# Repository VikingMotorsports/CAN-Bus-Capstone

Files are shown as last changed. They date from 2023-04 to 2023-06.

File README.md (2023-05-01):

<p align="center">

</p>

# VMS Can Bus Sensor Array

## Proposal Outline and Discussion

### 1. Executive Summary
Viking Motorsports is an EV racing team at PSU. They are a student organization and compete in
the Formula SAE competition against other schools nationally. Their overall goal is to design,
build and race a car every year. The electrical systems are complex, there are many systems that
must work in harmony with each other. There are also many possible single point failures that
can occur that will end our race.
Understanding this complex system is difficult, all of the information is locked away behind
body panels and wire insulation. The motivation of this project is to tap into that data to make it
easily accessible, this will enable rapid diagnostics and debugging. Additionally valuable data is
encoded in CAN by various off the shelf systems within the car. Accessing this data will also be
beneficial.
We want to deliver a network system that uses CAN to communicate system analytics from the
car's batteries and several other measured components and relay that information to the driver’s
display screen. The analytics will help troubleshoot any faults and errors in the operation of the
vehicle and allow for faster fixes on the race track. The system overall will consist of multiple
PCBs mounted in various locations on the vehicle to allow for sensor wires to relay the data to be
sent from each component to a data analyzer then get displayed on the screen.

<p align="center">

</p>

### 2. Background
The Viking Motorsports Team at PSU has been working on creating a fast, efficient, and
innovative EV to participate in the FSAE competition. Our project involves monitoring several
aspects of the EV via CAN and displaying the sensor outputs to the screen in the vehicle.
Monitoring these aspects via CAN will allow for efficient diagnostics of the EV systems and
make way for troubleshooting in the event of any failures.
The current electrical system is represented in the following diagram.

<p align="center">

</p>

For simplicity, all low voltage connections have been omitted, as well as some minor systems.
Currently, the only monitoring that is being done is battery temperature, and all monitoring done
by off the shelf systems within their own system. None of this information is accessible without
connecting a laptop to the various systems directly.
There are several different systems that need monitoring inside the EV. Primarily the HV (High
Voltage) system requires monitoring of the temperature sensors for the compartments that hold
the batteries. The temperature of the batteries affects the power output as well as the overall
performance of the car. Other components include the accumulator isolation relays, fuse, current
sensors, precharge and discharge system. The EV also requires monitoring of the LV (Low
Voltage) systems as well as the status of the pedal control system.
The industry standards have several requirements for CAN protocols being utilized in road
vehicles. Some of them include the following form ISO 11898:

* CAN specifies the high-speed physical media attachment (HS-PMA), including
HS-PMAs without and with low-power mode capability and those with selective wake-up
functionality.
* CAN specifies characteristics of setting up an interchange of digital information between
electronic control units of road vehicles equipped with CAN.

* CAN specifies the characteristics of setting up an interchange of digital information
between modules implementing the protocol’s data link layer.
Being able to monitor, process, and display these systems statuses will be extremely beneficial
for troubleshooting and overlay monitoring of the EV. The Formula SAE competition has very
specific requirements regarding galvanic isolation of the HV and LV systems in the EV. These
requirements need to be followed when developing our CAN system.

Data Flow Diagram
<p align="center">

</p>

It is important to note that the VMS team has not utilized the CAN bus system for monitoring
any sensor outputs in the past. However, even though the team has not implemented this system
yet, there are several other off the shelf devices that utilize CAN to help monitor and also
provide ability to alter the sensors and their calibration in order to get the best outcome from the
overall system. Haltech offers a wide range of CAN Bus devices along with the sensors that are
heavily used in the automotive industry, especially in DIY projects where factory engine
management systems fail to deliver proper results. Research in companies like Haltech as well as
other products like Vector used by Daimler can be beneficial for our project as well.

### 3. Project Overview
Our project starts with getting the STM32s to communicate with each other in order to relay information 
from one device to another. Each STM32 in our network will act as a CAN hub
utilized to relay information from a specific component cluster on the vehicle. We then want to
determine the protocols that allow data from the sensors to be received through the CAN
transceivers.

We then have to design individual PCBs for each of the CAN hubs that hold the STM32s, the
CAN transceivers and other peripheral components for the sensors to operate on the vehicle as
well.

Using the STM32CubeIDE and C programming, we have to code each of the microcontrollers to
log the data received from the CAN transceivers and relay them to the main Data Translator hub.
The Data Translator further encodes the data to be read by a RaspberryPi via I2
C which is used to display the data on the screen. We want the CAN system to be able to 
collect sensor outputs from different components of the
EV, send them to a central control hub, which processes the sensor readouts to legible
information for the user and outputs to a screen via the CAN adapter.

### 4. Product Design Specification

#### 4.1 Concept of Operation / User stories
Our goal for this project is to provide several different CAN modules that can be connected to
different sensors on the EV components and the placement of these modules provides flexibility
and easy integration along with the rest of the parts on the EV. Since the EV has restraints for
weight, countless other things, the placement of our modules is very important. These modules
are connected to the sensors on the vehicle and thus take the sensor readouts when the EV is
operated. The CAN module thus sends the readouts to the central control hub which is another
module that we create. This central hub encodes the sensor outputs and then sends them to the
LCD display on the car via a CAN Adapter.

As mentioned earlier, these modules are constructed specifically for the VMS EV and would for
the most part only work for our specific application since the placement on the devices, types of
sensor, variation in sensor outputs and the process to encode them would vary from one vehicle
to another. Thus the VMS team and their intermediate sponsors would be our main users and
stakeholders in this project.

It is important to note that the vehicles built by the VMS team in the past have not had any CAN
bus system utilized for monitoring and diagnostics. All previous troubleshooting was done in the
event of a system failure and the panels had to be taken apart to look at the individual
components and sensors to determine the source of error. The CAN bus allows the electricians on
the VMS team to simply use the LCD display and examine the readouts from the sensor in the
event of the failure. This speeds the time it takes them to fix the car and get it back in the race at
the FSAE competition. At the time the scope of our design concludes with relaying the data on
the display screen. However, the project can be continued in the future to use the CAN Adapter
to output the data logs to a laptop. There is also room in the future to be able to act upon the
information received via CAN. For example, the ability to do system shutdown in the event of a
component failure or out of range sensor reading can be a very effective addition to the overall
safety of the vehicle.

In our case, since the sponsor is the primary user for our project, we want to follow the timeline
of the rest of the EV build. Although we are not able to act upon the readouts we get from the
sensor, we are merely monitoring them. However, there are products available in the market that
allow for calibration and adjustment via USB connection to the CAN and sensors. This can be
looked into upon future development of our project. Each of the CAN hubs will also act as data
loggers as the microcontrollers will pull the data from the CAN bus, hold and store it.

As the rest of the members on the VMS team work on the other components that make the EV
work, we want to work alongside their progress so as to make the integration of the CAN Bus
more efficient and avoid any delays. We want the individual modules of the CAN Bus to be a
plug and play system which can be routed along with the rest of the wiring on the EV. Although
the design of the CAN Bus will be new for this year's EV, considering the fact that the VMS
team has to build a new vehicle from scratch every year, they might be able to utilize some of the
code and hardware and expand on the design of the CAN Bus for any future builds. Our goal is
to create a smoothly integrated monitoring system system that is seamless with the rest of the EV
build.

#### 4.2 Stakeholders
Our project was proposed by Braeden Hamson, lead electrician on the VMS team. Him, along
with several other key members on the team have been putting in countless hours in researching,
developing, constructing, testing, and then improving the iterations of the EV. We are designing
and constructing the CAN bus based on their requirements and working with them to create
smooth integration of the CAN Bus into the EV. However we feel that there can be several other
stakeholders in our project. The project team including Alice Ma, Braeden Hamson,
Jade Nguyen, and Pushpesh Sharma, want to create something that leaves room for future
growth and improvement. The EV inspectors that are part of the FSAE competition should also
be considered solid stakeholders in this project as their judgment and criticism can be beneficial
to the development of our project. But for the most part, the EV team at PSU will help integrate
its system, utilize it during the testing phase of the vehicle as well as on the track during the
competition. Upon the success of this project, we hope that the VMS team is able to use the
system for future use and add more features that helps the EV perform better in the upcoming
competitions.

#### 4.3 Requirements and Specifications
As mentioned earlier, we want to adhere to the requirements of the EV overall when designing
and constructing our CAN Bus systems. We want to follow any necessary restraints set by the
FSAE competition guidelines so as to avoid any delays and provide smooth integration of our
systems with the rest of the vehicle. Thus most of our requirements for this project are based on
the number of sensors and components that we want to read and monitor for the management of
the EV. Other requirements are based on what components we utilize in our project in order to
stay on budget and provide smooth integration when the time comes.

* Must be powered from 12V and/or 5V and tolerate a +/- 2V fluctuation
* When a board interacts with HV (350VDC) all HV components must be galvanically isolated from LV systems
* Must send data to a central data logging device connected to the CAN Bus
* Must use appropriate CAN Bus arbitration
* The team must cooperate with other members of the VMS team to ensure system compatibility
* Should follow accepted methods to protect devices on a CAN Bus
* Should use STM32 microcontrollers
* May monitor status of shutdown switches
* Should transmit data at a rate appropriate for the specific measurement
* Should monitor the following systems, in order of priority:
  * AIR+, AIR-, and precharge signals
  * APPS, BSPD, IMD, BMS OK, SDC status
  * Tractive system voltage, tractive system current
  * LV system voltages
  * Orion BMS 2 data
    * Battery state of charge
    * Tractive system power output
    * Battery voltage
    * Battery current
  * Cascadia Motion PM100DX data
    * Individual motor power
    * Inverter mode (running, fault, precharging etc.)
    * Relay outputs (used to detect wiring faults)

#### 4.4 Deliverables
This critical section specs out what you're going to deliver to the industry sponsor by the end of
your capstone. This must include:

* Project proposal
* Weekly Progress Reports
* Final Report
* ECE Capstone Poster Session poster
* Travel with the VMS team to Michigan to attend the FSAE competition. It is held on June 14-17 (travel and other expenses are covered)
* Detailed design documentation, explaining how your what your design does, how your design works, and why you made the decisions you did
* Simulations, including both the simulation inputs and outputs
* Electrical CAD: Schematics and board layouts, including output files (Gerbers, PDFs, etc)
* Bill of materials and pricing
* Version control, including checked in previous revisions of your design (e.g., a Git repo).
* Individual PCBs with 3D printed housings for each of the boards.
* Functional code for STM32CubeIDE for the individual CAN hubs.

#### 4.5 Initial product design
Our current progress on this project consists of setting up software for the microcontroller
that we will be using. We have decided to use STM32 along with the STM IDE to be able
to take the sensor outputs from each component and then convert the values to send to the
CAN Adapter which in the end gets displayed on the screen. We have also started
working on the schematics for the PCBs that contain the STM32 microcontroller. These
schematics contain the microcontroller itself along with the peripheral components that
are necessary. We are also working on getting multiple STM32s to communicate with
each other as the end goal would be to have several different boards placed in close
proximity to the location of the sensor and have them send the sensor output to one main
microcontroller board via CAN that processes the input and sends it to the CAN adapter.

* Hardware architecture
<p align="center">

</p>

* Software architecture
  * C, STM32CubeIDE

* User interface / experience

User Story: In the lab, the user is assembling the car, they test a certain feature
and see that it does not function as intended. They can then go to the driver’s
steering wheel, use the on wheel controls to enter a maintenance menu that will
display all measured parameters by the CAN system. They can then use this
information to find the problem. For instance, the car is powered on, but HV will
not engage. The user looks at the data from the wheel and sees that the pedal
control board is indicating a signal out of range of the pedal controller.
Investigating the sensor connections they find the sensor unplugged. They plug
the sensor in and the system indicates the sensor is in range. The car then turns on.

* Other considerations

Electric vehicles are electrically noisy. Shielded wire will be used for long wire
runs around the vehicle.
The battery pack contains up to 350V, galvanic isolation will separate the boards
that are close to HV systems from the rest of the systems.

* Back up plans

The overall goal of this project is to create an easily debugged vehicle. If our
plans totally crash and burn there’s nothing wrong with creating a 1960’s aesthetic
by throwing a ton of blinking indicators around the car for debugging.
A step up from that is to use Arduinos and create a similar but less complex
system for debugging.
The only aspect of this project that must be completed are the battery temperature
monitors. Without this system the vehicle will not be allowed to race.

#### 4.7 Verification plans
One of the biggest concerns with this project is the final integration of the CAN Bus with the rest
of the components on the EV. We want to make sure that the system is able to successfully take
the readouts from the sensors on the EV and encode them to be displayed on the screen. A lot of
testing would be required to determine that the system is operating correctly.

The system will meet requirements if it can successfully read the temperature sensors in the
battery modules and display them on the LCD. We may program the STM32s to encode the
readout from the temperature sensors and determine whether it falls within the specific range for
the battery to have optimal performance based on the requirements of the VMS team. Test: Does
the LCD display the temperature of the specific battery module? Does it indicate when the
temperature gets above a threshold range?

We are also going to test multiple STM32s to see if they can communicate with each other
through the CAN network by sending messages from component A to component B, then from
component B to component C, or until one goes to bus-off condition. we will determine if the
system can analyze the error registers of the node as a means of measuring bus performance of a
transceiver.

### 5. Project Management Plan

#### 5.1 Timeline, with milestones
The timeline for our project needs to be aligned with that of the VMS team in order to finish the
EV in time for the FSAE competition. Our sponsor wants to have a working CAN Bus system by
the end of the ECE 412 course in order to leave ample time for system integration with the rest
of the EV as well as the testing, and troubleshooting phases.
See Google Sheets below for a tentative timeline

Click [here](https://docs.google.com/spreadsheets/d/1ESAUExDIhOSoRCvXFfbeXnNjUjRd7T-Y1ovpI8qUFuQ/edit#gid=0) to view tentative project timeline

#### 5.2 Budget and Resources

The budget for our project is combined with that of the overall VMS budget for the EV. Our
main costs are going to dependent on the following:

● Number of STM32s used and their cost
● Cost of peripheral components for the microcontrollers
● Manufacturing costs of the PCBs for the STM32s and the peripheral components
● Wiring for the integrated boards via CAN.

The VMS team has kindly Altium to design the PCBS for the CAN modules. Most other
components would be ordered from DigiKey or may already be available in the VMS inventories
as they have been working on multiple vehicles in the past. The VMS team has also provided a
work area along with the rest of the team members as resources for our project.

#### 5.3 Intellectual Property Discussion
A goal of this capstone is to provide a framework to future teams to build more advanced CAN
systems. Therefore all IP generated here will be completely open source, and will be readily
available to future teams. The license used for the repository and the project overall is the MIT License
<p>

</p>

#### Faculty Advisor Approval
Advisor Name: Roy Kravitz |
Signature: e-approved by Roy Kravitz (rkravitz@pdx.edu) |
Date: 27-Feb-2023

#### 5.4 Team and Development process

* Alice Ma: Project manager and Programming lead. Working on programming STM32 for
sending and receiving CAN messages.
* Braeden Hamson: VMS electrical lead. CAN capstone technical lead. Understands the
vehicle systems and the interface between the CAN system and the rest of the systems of
the car.
* Jade Nguyen: Working with Alice on setting up a CAN bus using the STM32
microcontroller, providing simple C code to read and write to the CAN bus and send it to
the transceiver.
* Pushpesh Sharma: Working on PCB schematics and using Altium to set up schematics,
footprints, PCB files and manufacturing files for several boards for CAN Bus.

* Collaboration tools: Notion for team tasking and note taking, Discord for every comms
and virtual meetings, Github for code and boards, Google Suite for deliverables.

### Project Sponsor 

<p align="center">

</p>

Viking Motorsports (VMS) is a student group focused on designing and building formula race
cars from the ground up. Every year, VMS competes in Formula SAE, which is a worldwide
collegiate competition created by SAE International.

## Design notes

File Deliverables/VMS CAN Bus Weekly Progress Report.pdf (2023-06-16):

### VMS CAN Bus Capstone Weekly Progress Report

Report date: Jan 20, 2023

- Last Week (times in hours)
- Team Review
■ We planned for a short check-in meeting on Mondays and a working meeting on Thursday.
■ Had a meeting with the faculty advisor.
■ Gave everyone a role for the project.
■ Got into the VMS lab to look at the physical car and get supplies (STM32) needed to start coding.
- Braeden Hamson
■ Contacted, via email, the faculty advisor, Roy, to introduce us as a team (0.5)
■ Gathered a list of sensors we need to get signals from (2)
■ Researched about the STM32 (2)
- Pushpesh Sharma
■ Researched about CAN (3)
- Alice Ma
■ Planned our meetings with Roy via email (.5) ■ Researched about CAN (3)
- Jade Nguyen
■ Researched about CAN (3)
- Next week
- Team Plan
■ Meeting with sponsors (other VMS team members) in person to get their opinion and requirements on the project.
- Braeden Hamson
■ Order STM32 enough for the project (1)
■ Gathered a list of sensors we need to get signals from (2)
■ Start testing the CAN transceivers and STM32 for sending CAN messages.
- Pushpesh Sharma
■ Set up our collaboration site on Github and added structure (3)
■ Learn about Altium (3)
- Alice Ma
■ Start programming the STM32 and get familiar with the IDE (3)
■ Planned meeting with faculty advisor for bi-weekly Friday meetings (.25) ■ Start the template for the weekly progress reports. (1)
- Jade Nguyen
■ Learn about CAN protocol (3)
■ Start programming the STM32 and get familiar with the IDE (3)
- Blocked
- Braeden Hamson
■ Need to wait until more STM32 to get here so we can all start programming.
- Pushpesh Sharma
■ Haven’t gotten access code for the Altium program
- Alice Ma
■ No blocks
- Jade Nguyen
■ No blocks

Report date: Jan 27, 2023

- Last Week (times in hours)
- Team Review
■ Originally planned to have a central STM32 that collected a lot of the data, but now we will use Raspberry pi.
■ Everyone has done good basic research of the topic
- Braeden Hamson
■ Tested the STM32 boards and CAN transceivers (3) ■
- Pushpesh Sharma
■ Finished with Altium tutorials (3)
■ Started Altium files for Accumulator Schematic.
- Alice Ma
■ Was able to write code to the STM32 board (3)
- Jade Nguyen
■ Researched about CAN (3)
- Next week
- Team Plan
■ We should divide our time as the programming team and the circuit design team.
- Braeden Hamson
■
- Pushpesh Sharma
■ Design schematics, collect part specs for connectors and mates, work on symbol and footprint of STM32. Find the thermistor part. Design the voltage divider circuit.
- Alice Ma
■ Be able to communicate between two STM32 through CAN protocol. (5)
- Jade Nguyen
■ Learn about CAN protocol (3)
■ Start programming the STM32 and get familiar with the IDE (3)
○
- Blocked
- Braeden Hamson
■ Need to wait until STM32 to get here so we can all start programming.
- Pushpesh Sharma
■ Waiting final specs on STM32, finding correct thermistors for the team.
- Alice Ma
■ No blocks
- Jade Nguyen
■ No blocks

Report date: Feb 3, 2023

- Last Week (times in hours)
- Team Review
■ Decided on using another STM32 dev board due to our current one only works with CANfd instead of CAN which makes stuff more complicated.
■ We will order more boards.
- Braeden Hamson
■ Redesigned pedal control board, integrated STM32 (10)
■ Continued learning STM32 coding (3)
- Pushpesh Sharma
■
- Alice Ma
■ Attempting to send CAN messages between two STM32 from CubeIDE(6)
- Jade Nguyen
■ Trying the code for sending data inside the loopback mode (3)
- Next week
- Team Plan
■ We need a CAN Architecture Documentation.
■ Have the CAN communication between CAN STM32 down ■ Order the new STM32 boards
■ Plan for error handling for the CAN bus.
- Braeden Hamson
■ Learn STM32 coding
- Pushpesh Sharma
■ Continued design for Accumulator boards. Meeting with E-train team to discuss board placement and any restrictions for components size or placement
- Alice Ma
■ Communication between the new STM32 boards through the CAN bus
■ Update gantt chart
- Jade Nguyen
■ Learn about the configuration and filter of CAN devices
■ Starting code for communicating between 2 STMs
○
- Blocked
- Braeden Hamson
■ Not enough boards to go around.
- Pushpesh Sharma
■ Board placement and component preferences for SAE rules
- Alice Ma
■ Need new STM32 boards.
- Jade Nguyen
■ Waiting for more STM32

Report date: Feb 10, 2023

- Last Week (times in hours)
- Team Review
■ Was able to get new STM32s and start coding! ■ Getting board schematics started.
- Braeden Hamson (10)
■ Helped others with projects
■ Worked on accumulator master board
- Pushpesh Sharma
■ Accumulator Board redesign with new placement and pivoting to different size.
■ Researching new components and sending inquiries for component customization.
- Alice Ma
■ Coding the new STM32 for CAN communication between two STM32, not achieved yet (6)
- Jade Nguyen
■ Got blinking LED for receiving message by the Loopback mode, but can’t check the exact message that was sent. (3)
■ Learnt about Can filter and Can ID code (1)
- Next week
- Team Plan
■ Achieve CAN communication between two STM32s to send and receive CAN messages.
■ Update project proposal
- Braeden Hamson
■ Determining HV and LV isolation method for accumulator boards
- Pushpesh Sharma
■ Continue work on PCB schematics for Accumulator boards for front and backside of batteries
- Alice Ma
■ Write code for sending messages from 1 STM and receiving messages for another STM.
- Jade Nguyen
■ Write code for sending messages from 1 STM and receiving messages for another STM.
- Blocked
- Braeden Hamson
■ None
- Pushpesh Sharma
■ Waiting for clear comms on the size of connectors used for all wires. Waiting comms from manufacturer for customized thermistors for batteries.
- Alice Ma
■ I have no idea why they are not sending CAN messages.
- Jade Nguyen
■ No block

Report date: Feb 17, 2023

- Last Week (times in hours)
- Team Review
■ Midterm week so not much was done during the week
- Braeden Hamson
■ Came to the conclusion that HV LV isolation will need to be done with spacing as any other method is overly expensive.
- Pushpesh Sharma
■ Continue work on PCB schematics for Accumulator boards for front and backside of batteries
- Alice Ma
■ Got the STM32 to send and receive messages through the CAN bus!(5)
- Jade Nguyen
■ Wasn't able to make the STM receive messages even when the data was sent. (7)
- Next week
- Team Plan
■ Week 7 and week 8 to prototype and finalize design for the board.
■ Before spring break, we should have the boards ready to be sent out.
- Braeden Hamson
■ Work with an accumulator designer to figure out a new way to reduce the large number of wires in the accumulator.
- Pushpesh Sharma
■ Continue work on PCB schematics for Accumulator boards for front and backside of batteries
- Alice Ma
■ Research what messages to send on the CAN bus and how to send different messages.
- Jade Nguyen
■ Continue working on STM communication
- Blocked
- Braeden Hamson
■ None
- Pushpesh Sharma
■ Waiting for clear comms on the size of connectors used for all wires. Waiting comms from manufacturer for customized thermistors for batteries.
- Alice Ma
■ No block
- Jade Nguyen
■ Can’t get the messages from CAN bus

Report date: Feb 24, 2023

- Last Week (times in hours)
- Team Review
■ It was the snowpocalypse this week so we weren’t able to meet up and get more STM32 in person but we were able to meet online
- Braeden Hamson
■ Worked with an accumulator designer to figure out a new way to reduce the large number of wires in the accumulator.
- Pushpesh Sharma
■ Have further discussion with the e-train team on size and placement of PCBs inside the battery segments. Finalize measurements for our designs.
- Alice Ma
■ Was able to get the STM32 to print out what is being received on a serial monitor and now we can see what we are sending and receiving. (5)
- Jade Nguyen
■ Figure out one of the CAN transceiver was broken, that’s why the STM couldn’t receiving any messages from the CAN bus (6)
■ Got the STM communication by CAN bus (1)
- Next week
- Braeden Hamson
■ Focus on data translator board
- Pushpesh Sharma
■ Complete Schematic for top and bottom boards for Accumulator. Start on design for schematic for Accumulator Main board and Data Analyzer board.
■ Complete product spec for Thermistors and finalize invoice.
- Alice Ma
■ Achieve CAN communication between multiple STM32s and be able to give priority to each SMT32.
- Jade Nguyen
■ Get the code for the STMs both sending and receiving data at the same time.
■ Filter out STMs’ ID to only receive the data that we want.
■ Try the code for requesting data from other STMs
- Blocked
- Braeden Hamson
■ None
- Pushpesh Sharma
■ Weather conditions halting in-person time with the team to continue progress on schematics.
- Alice Ma
■ The snow didn’t allow me to get another STM32 for testing.
- Jade Nguyen
■ No block

Report date: Mar 3, 2023

- Last Week (times in hours)
- Team Review
■ Team continues to make progress on both hardware and software sides. Continued meetings with faculty advisor and industry sponsor for ways to improve and key factors that will help avoid delays.
- Braeden Hamson
■ None
- Pushpesh Sharma
■ Work on finding footprints for all components in the current boards. Top, Bottom and Shelf board have digikey files for footprint and 3D model to upload in Altium.
- Alice Ma
■ Was able to debug the reason why my STM32 were freezing when I plugged them in.
- Jade Nguyen
■ Got the STMs both sending and receiving data at the same time. (1)
■ Filter out STMs’ ID to only receive the data that we want. (1)
■ Can receiving data from multiple STMs (2)
- Next week
- Team Plan
■ Work hard
- Braeden Hamson
■ None
- Pushpesh Sharma
■ Continue finding, uploading the updating schematics for TOP, BOTTOM and SHELF boards with footprints before moving on with PCB layouts. Continue finalizing all other boards for this project
- Alice Ma
■ Measure different voltages and convert it to temperature.
- Jade Nguyen
■ Learning to use ADC in the STM32 to measure analog voltage ■ Figure out what data should be sent to the Data Translator
- Blocked
- Braeden Hamson
■ Sick
- Pushpesh Sharma
■ Information missing from other teams for components and parts going on Data Analyzer board. Pedal controller board being worked on by VMS team overall.
- Alice Ma
■ BUGGG
- Jade Nguyen
■ Can’t requesting data from other STMs (however, we try to keep sending and update information of the battery temp every 2 seconds)
■ Will go back to this if we need it in the future

Report date: Mar 10, 2023

- Last Week (times in hours)
- Team Review
■ Continued progress.
- Braeden Hamson
■ None
- Pushpesh Sharma
■ Continued work with footprints for Top, bottom and shelf boards. Work with Braeden on DXF files for PCB layouts
- Alice Ma
■ Read the voltage from the analog pin (2)
■ Set up multiple ADCs channel on STM32 using DMA (4)
- Jade Nguyen
■ Read the voltage from the analog pin (2)
■ Set up multiple ADCs channel on STM32 using DMA (4)
- Next week
- Braeden Hamson
■ None
- Pushpesh Sharma
■ Finalize all footprints for the 3 current boards before moving on with PCB layouts using DXF files from Braeden.
- Alice Ma
■ Send the measurements in CAN bus messages
- Jade Nguyen
■ Still working on measuring multiple analog voltages ■ Be able to send and receive data by CAN bus
- Blocked
- Braeden Hamson
■ Sick
- Pushpesh Sharma
■ Data Translator board still missing some key information before working on schematic.
- Alice Ma
■ Homework
- Jade Nguyen
■ Can’t convert ADC values to a real voltages in the interrupt callback loop

Report date: Mar 17, 2023

- Last Week (times in hours)
- Braeden Hamson
■ None
- Pushpesh Sharma
■ Finalized all footprints for the 3 current boards before moving on with PCB layouts using DXF files from Braeden.
- Alice Ma
■ Able to convert the outputs of the STM32 from the range of ADC values (0 to 4095) to the real voltages in the main while loop (2)
- Jade Nguyen
■ Be able to convert the outputs of the STM32 from the range of ADC values (0 to 4095) to the real voltages in the main while loop (2)
■ Got the STM to send data (analog voltage) from the thermistors connections to the CAN bus (3)
- Next week
- Braeden Hamson
■ None
- Pushpesh Sharma
■ PCB layouts starting for Top, Bottom and Shelf boards. DXF files received from Braden.
- Alice Ma
■ We need to get the code for the thermistors done and start dividing up the work for coding for the other PCBs
- Jade Nguyen
■ Get the STM32 could send and receive the data properly
■ Convert voltages to temperature
■ Start working on the mux in the main board, how does it work and be able to get information from it
- Blocked
- Braeden Hamson
■ Sick
- Pushpesh Sharma
■ Finals week.
- Alice Ma
■ Waiting for more CAN transceivers to build a new CAN bus board so we don’t have to take turn to keep it
- Jade Nguyen
■ Can’t receive the right information from the CAN bus
■ Waiting for more CAN transceivers to build a new CAN bus board so we don’t have to take turn to keep it

Report date: Mar 24, 2023

- Last Week (times in hours)
- Team Review
■ We need to catch up during spring break
■ CAN transceivers finally arrived meaning we can divide up the work now.
- Braeden Hamson
■ DXF files for Top and Bottom Boards for PCB Layouts
■ Made footprints for accumulator segment board components
■ Began schematic for data translator/datalogger board.
- Pushpesh Sharma
■ Finalize all footprints for the 3 current boards before moving on with PCB layouts using DXF files from Braeden.
- Alice Ma
■ Was able to convert raw ac voltage data to DC voltage and send it through the CAN bus. [7]
- Jade Nguyen
■ Got the right information from the CAN bus [4]
■ Was able to to convert voltages from the battery segments to temperature
- Next week
- Braeden Hamson
■ Focus on system integration. I’ll be working to make sure that we’re not missing any systems and that we’re on track to meet our goals. I’ll make a detailed list of tasks and goals.
■ Finish data translator schematic
■ Create an unrouted pcb and layout components for the DT. Send the 3d model to the designer responsible for its placement in the car. Adjust if needed, and route.
- Pushpesh Sharma
■ Continuing work on PCB layouts for the boards we have in progress. Working on schematic for Data Analyzer board with new information from the VMS team.
- Alice Ma
■ Start working on the data translator.
- Jade Nguyen
■ Working on the selected bits for the MUXs in segments board
- Blocked
- Braeden Hamson
■ Translation issues with thermistor suppliers around connector terminology.
- Pushpesh Sharma
■ Spring break
- Alice Ma
■ Spring break
- Jade Nguyen
■ Spring break

Report date: Mar 31, 2023

- Last Week (times in hours)
- Braeden Hamson
■ Worked on accumulator boards
- Pushpesh Sharma
■ New information VMS team requiring complete redesign of Top / Bottom and Accumulator shelf board
- Alice Ma
■ Attempting to communicate with two STM32s through I2C (6)
■ Talked with the guy in charge of the RBP to ask for help on I2C (3)
- Jade Nguyen
■ Configured the pins and the logic code for the 8x1MUXs and 2x1MUXs on the segment board [6]
- Next week
- Braeden Hamson
■ Finalize accumulator board
- Pushpesh Sharma
■ Meetings with VMS team for new dimensions and changes to 3 boards. Redesign, routing and PCB layouts.
- Alice Ma
■ Have I2C communication working on STM32
■ Figure out whether data translator board is master or slave
- Jade Nguyen
■ Checking temp to make sure it is under 60C and send signal to BSM ■ Start working with messages from BSM
- Blocked
- Braeden Hamson
■ Waiting on accumulator designer
- Pushpesh Sharma
■ Waiting further confirmation from VMS team.
- Alice Ma
■ Could not get I2C to work for some reason.
- Jade Nguyen
■ None

Report date: Apr 7, 2023

- Last Week (times in hours)
- Braeden Hamson
■ Finished segment boards
- Pushpesh Sharma
■ Completed redesign for Top / Bottom / and Shelf boards with new layouts and PCB designs
- Alice Ma
■ Was able to establish communication between I2C as master transmit and slave receive
■ Started on implementation with CAN running at the same time.
- Jade Nguyen
■ Got the OK signal send to BSM
- Next week
- Braeden Hamson
■ Send boards to FAB
- Pushpesh Sharma
■ Finalize these boards and develop fabrication files to send boards out for manufacturing.
- Alice Ma
■ Data logger needs to be slave and RBP master request receive
- Jade Nguyen
■ Still work on the BSM signals
- Blocked
- Braeden Hamson
■ None
- Pushpesh Sharma
■ Any further information from the VMS team before finalization.
- Alice Ma
■ Problem with CAN and IC2 not working at the same time
- Jade Nguyen
■ The STM32 does not enough GPIO pins for 9 signals coming at the same time

Report date: Apr 14, 2023

- Last Week (times in hours)
- Braeden Hamson
■ Sent boards to fab
- Pushpesh Sharma
■ Boards finally finalized. Started creating fab gerber files for Top, Bottom and Shelf boards.
- Alice Ma
■ I2C is Baddddd
- Jade Nguyen
■ Cut out the pins that used to print out what is being sent on a serial monitor and use it for the BSM
■ Receiving to many signals from BMS affects the pins that reading temperature from the thermistors
- Next week
- Braeden Hamson
■ Work on “PDAC” accumulator board, main contactor controller
- Pushpesh Sharma
■ Gerber files created. Create BOM files for components on Top, Bottom, and Shelf boards for the VMS team to order. Start working on the Data Translator Board.
- Alice Ma
■ I don’t know what to do with I2C
- Jade Nguyen
■ Still working on the BSM signals
- Blocked
- Braeden Hamson
■ None
- Pushpesh Sharma
■ None
- Alice Ma
■ None
- Jade Nguyen
■ The inputs Pins for the thermistor now outputs some voltages, I don’t know where it came from

Report date: Apr 21, 2023

- Last Week (times in hours)
- Braeden Hamson
■ Working on PDAC
- Pushpesh Sharma
■ Top, Bottom, and Shelf board gerber files sent to the VMS team to send to fab. BOM file for these boards created and sent to the VMS team. Files received from Braeden for DataTranslator board.
- Alice Ma
■ Research about I2C communication
- Jade Nguyen
■ Figured out that there were 3 pins can not be used to read the signals from BMS ■ Decided to reduce the number of signals gonna run to the accumulator board to 6
- Next week
- Braeden Hamson
■
- Pushpesh Sharma
■ Continued work on DT board based on changes from the VMS team. Needs schematics updated with actual parts, PCB layout finalized and routing done.
- Alice Ma
■ Work on I2C to send message to Raspberry Pi
- Jade Nguyen
■ Finishing the code for the accumulator board
- Blocked
- Braeden Hamson
■ None
- Pushpesh Sharma
■ None
- Alice Ma
■ None
- Jade Nguyen
■ None

Report date: Apr 28, 2023

- Last Week (times in hours)
- Braeden Hamson
■ Working on PDAC
- Pushpesh Sharma
■ Continued work on DT board with routing and components. Needs finalized then gerber files created.
- Alice Ma
■ Working on CAN filters with Braeden to be able to filter for three specific headers from the car.
- Jade Nguyen
■ Insteads of using ADC to receiving messages from BMS, we changed to shifts register so we can read up to 16 signals serially
- Next week
- Braeden Hamson
■
- Pushpesh Sharma
■ DT board finalized with gerber files created. BOM for that board too.
- Alice Ma
■ Establish I2C communication
- Jade Nguyen
■ Working on the code for the shift register
- Blocked
- Braeden Hamson
■
- Pushpesh Sharma
■ I think the DT board will need an overhaul based on new information from VMS
- Alice Ma
■ One of my STM32 could not use CAN for some reason so I needed to use another STM32
- Jade Nguyen
■ None

Report date: May 5, 2023

- Last Week (times in hours)
- Braeden Hamson
■ Finished PDAC, sent to FAB
- Pushpesh Sharma
■ Continued work on DT board. Routing done, PCB layout finalized. Waiting approval before gerber files created. New information from VMS team. DT board needs few things redesigned. Board needs schematic lookover with entire capstone team for confirm pin assignments.
- Alice Ma
■ I2C communication doesn’t work so we need to switch to UART.
- Jade Nguyen
■ Got the shift register work well, tested by oscilloscope to get a suitable frequency
- Next week
- Braeden Hamson
■ Hope to get segment boards
- Pushpesh Sharma
■ DT board fixed based on new discoveries. Schematic updated, PCB layout changed and routing fixed. Gerber files created. Board sent out. BOM being worked on.
- Alice Ma
■ Write a program for communication between UART to raspberry pi
- Jade Nguyen
■ Starting with the pedal control code to get messages from the motor controller via CAN
- Blocked
- Braeden Hamson
■
- Pushpesh Sharma
■ None
- Alice Ma
■
- Jade Nguyen
■ None

Report date: May 12, 2023

- Last Week (times in hours)
- Braeden Hamson
■ Assembling segment boards
- Pushpesh Sharma
■ Gerber files for all boards sent to the VMS team to be sent for manufacturing. BOMs for each board sent to VMS team to be ordered as well.
- Alice Ma
■ Establish UART communication to Raspberry Pi
- Jade Nguyen
■ Working on the code for the filters of the CAN to get the needed messages.
- Next week
- Braeden Hamson
■ Assess segment boards
- Pushpesh Sharma
■ Start on documentation while waiting on PCBs to arrive. Rough draft of final report, capstone poster. Prep for assembly of boards. Documentation continued with Poster Design and Final Report.
- Alice Ma
■ Organize all the data needed to be sent to UART raspberry pi
- Jade Nguyen
■ Still working on the filters and decoding message from the motor controller
- Blocked
- Braeden Hamson
■ Put wrong fuse footprint on segment boards
- Pushpesh Sharma
■ Fab time for boards
- Alice Ma
■ None
- Jade Nguyen
■ Stuck on the logic for the filters

Report date: May 19, 2023

- Last Week (times in hours)
- Braeden Hamson
■ Project management, helping with projects
- Pushpesh Sharma
■ All boards sent to be fabricated. All parts ordered as well. Boards will need to be assembled as soon as they come in.
- Alice Ma
■ Format the data that will be sent to the raspberry pi
- Jade Nguyen
■ Alice helped to get the filters work
- Next week
- Braeden Hamson
■ Designing boards
- Pushpesh Sharma
■ Start assembling boards. Components are coming in as well. Documentation continued with Poster Design and Final Report.
- Alice Ma
■ Final testing with the raspberry pi to send all the data and format.
- Jade Nguyen
■ Decoding the messages from the motor controller to meaningful number, store it to local variable for the other capstones group to use
■ Combining our code with their code.
- Blocked
- Braeden Hamson
■ None
- Pushpesh Sharma
■ Accumulator Main Board was not ordered due to miscommunication. Still waiting on that one to be ordered.
- Alice Ma
■ Waiting to test on the board
- Jade Nguyen
■ None

Report date: May 26, 2023

- Last Week (times in hours)
- Braeden Hamson
■ Finishing pedal control board assisting with all projects
- Pushpesh Sharma
■ Started assembling boards with Braeden. Top and Bottom Segment boards first using stencils. Polycarb segments are available for mounting those
- Alice Ma
■ Finished testing the UART communication to the raspberry pi with Nate. Everything worked!!
- Jade Nguyen
■ Tried to understand the code from the other group
■ Got the code working together but we haven’t got the result that we want
- Next week
- Braeden Hamson
■ Sending pedal control to FAB
- Pushpesh Sharma
■ Continuity tests for all boards as they get assembled. Data Translator board assembled as it arrives. Documentation continued with Poster Design and Final Report
- Alice Ma
■ Help with final report and work start finalizing the data translator code
- Jade Nguyen
■ Work on final report, finish the code for the pedal controller
- Blocked
- Braeden Hamson
■ None
- Pushpesh Sharma
■ Accumulator Main board still needs ordered. May have to be sent to a local manufacturer.
- Alice Ma
■ None
- Jade Nguyen
■ Need to check APPS_OK signal and send to the CAN bus but still lost in the code

Report date: Jun 2, 2023

- Last Week (times in hours)
- Braeden Hamson
■ Assembling boards.
- Pushpesh Sharma
■ Assembled Top and Bottom Segments completely with thermistors and connectors. Kapton tape to keep thermistors in place. Data Translator Board assembled by Braeden.
- Alice Ma
■ Help assemble the data translator with Braeden.
- Jade Nguyen
■ Got the pedal controller code to work well. Be able to received messages from the motor controller and send checking signal to Data translator via CAN
■ Tested it on the real pedal control board in the EV
- Next week
- Braeden Hamson
■ Assembling boards
- Pushpesh Sharma
■ Hopefully Accumulator Main Board comes in. That will be assembled, tested and wired. Wiring harness will be created for each board as it gets integrated into the existing chassis for CAN testing. Documentation continued with Poster Design and Final Report
- Alice Ma
■ Assigning headers to CAN messages that will be received. Working on posters.
- Jade Nguyen
■ Working the final report
- Blocked
- Braeden Hamson
■
- Pushpesh Sharma
■ Waiting on Oshpark for Accumulator Main Board.
- Alice Ma
■ None
- Jade Nguyen
■ Waiting for Accumulator Main Board.

Report date: Jun 9, 2023

- Last Week (times in hours)
- Braeden Hamson
■ Assembling boards
- Pushpesh Sharma
■ Accumulator Main Board finally arrived. Board assembled and continuity test complete. Wiring will need to be done with the rest of the team during the integration process.
- Alice Ma
■ Decoding the messages received from the Motor Controller.
- Jade Nguyen
■ Assembled and made harnesses that connect battery segment and accumulator board (only have 1 segment board)
■ Ran and tested the code, missing 5V trail to run the board
■ Decided to connect to the laptop for the demo
- Next week
- Braeden Hamson
■ Assembling and testing boards
- Pushpesh Sharma
■ Wiring for Top and Bottom Segments as well as the Accumulator Main Board for testing. Documentation continued with Poster Design and Final Report
- Alice Ma
■ Finalizing the changes made to the code for the data translator
- Jade Nguyen
■ Working on the final report
- Blocked
- Braeden Hamson
■ None
- Pushpesh Sharma
■ None
- Alice Ma
■ Boards not complete
- Jade Nguyen
■ None

Report date: Jun 16, 2023

- Last Week (times in hours)
- Braeden Hamson
■ Tidying car wiring, helping with debugging. BODGING BODGING BODGING, dying on the inside.

■

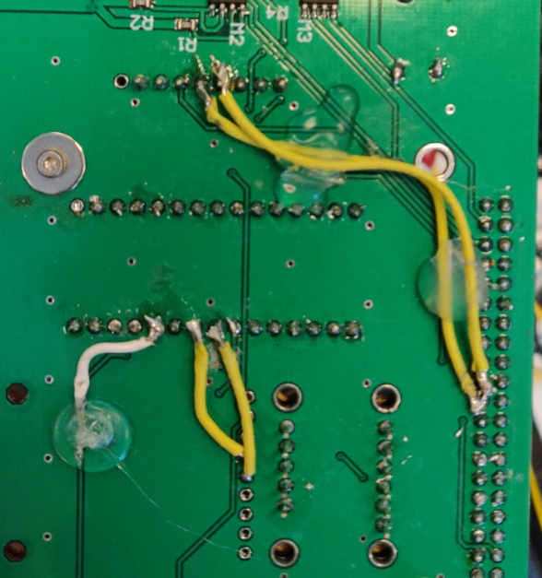
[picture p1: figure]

- Pushpesh Sharma
■ Complete documentation with Poster Design and Final Report. Assist with integration and testing. Prep presentation for VMS team with Roy.
- Alice Ma
■ Integration all the boards and final edits and testing for the boards
- Jade Nguyen
■ Integration all the boards together
- Next week
- Braeden Hamson
■ Laying around, chips, zoning out, finding an effigy to burn for a cathartic release.
- Pushpesh Sharma
■ Final Report. VMS team presentation with Roy. Poster Presentation.
- Alice Ma
■ Nothing 🙂
- Jade Nguyen
■ None
- Blocked
- Braeden Hamson
■ None
- Pushpesh Sharma
■ None
- Alice Ma
■ A lot of board problems
- Jade Nguyen
■ None

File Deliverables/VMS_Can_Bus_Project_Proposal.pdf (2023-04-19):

Alice Ma
Braeden Hamson
Jade Nguyen
Pushpesh Sharma
ECE 412 Senior Project Dev
Winter 2023 | 1

Proposal Outline and Discussion

### 1. Executive Summary

Viking Motorsports is an EV racing team at PSU. They are a student organization and compete in the Formula SAE competition against other schools nationally. Their overall goal is to design, build and race a car every year. The electrical systems are complex, there are many systems that must work in harmony with each other. There are also many possible single point failures that can occur that will end our race.

Understanding this complex system is difficult, all of the information is locked away behind body panels and wire insulation. The motivation of this project is to tap into that data to make it easily accessible, this will enable rapid diagnostics and debugging. Additionally valuable data is encoded in CAN by various off the shelf systems within the car. Accessing this data will also be beneficial.

We want to deliver a network system that uses CAN to communicate system analytics from the car's batteries and several other measured components and relay that information to the driver’s display screen. The analytics will help troubleshoot any faults and errors in the operation of the vehicle and allow for faster fixes on the race track. The system overall will consist of multiple PCBs mounted in various locations on the vehicle to allow for sensor wires to relay the data to be sent from each component to a data analyzer then get displayed on the screen.

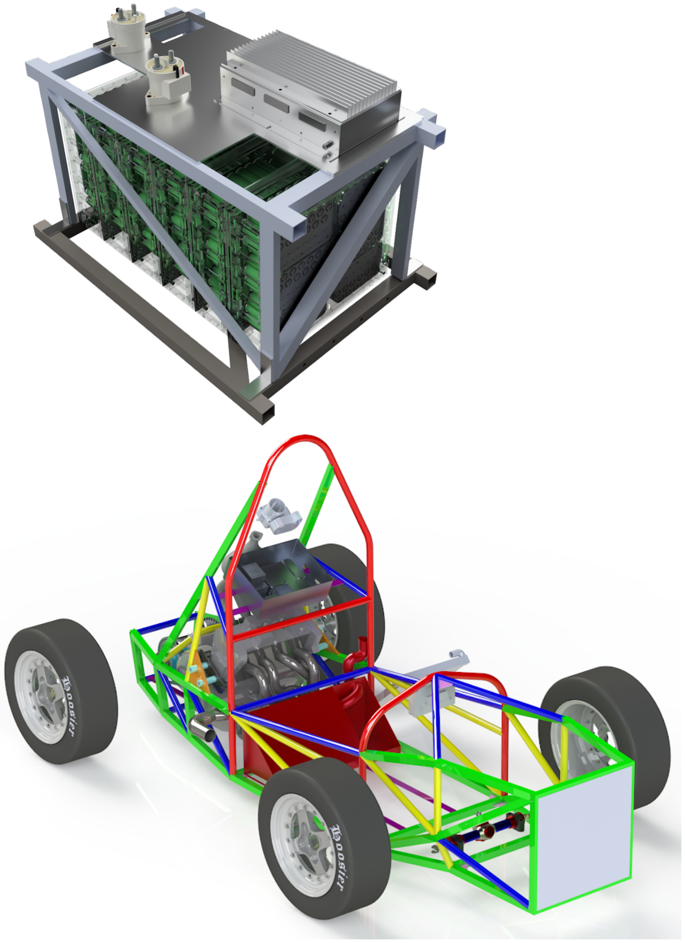
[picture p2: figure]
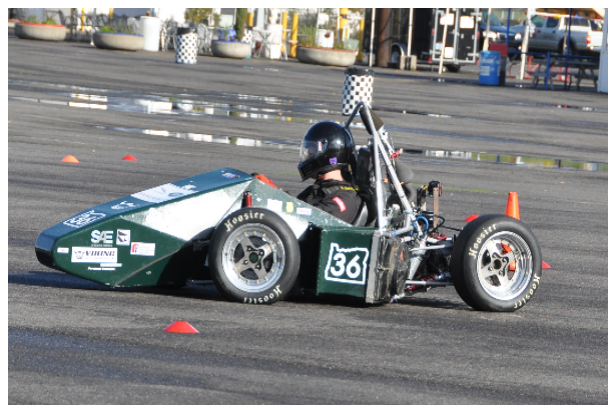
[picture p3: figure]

### 2. Background

The Viking Motorsports Team at PSU has been working on creating a fast, efficient, and innovative EV to participate in the FSAE competition. Our project involves monitoring several aspects of the EV via CAN and displaying the sensor outputs to the screen in the vehicle. Monitoring these aspects via CAN will allow for efficient diagnostics of the EV systems and make way for troubleshooting in the event of any failures.

The current electrical system is represented in the following diagram.

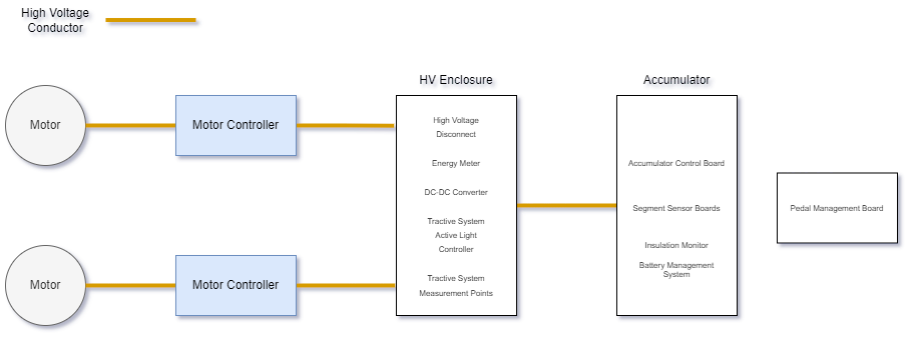
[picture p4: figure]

For simplicity, all low voltage connections have been omitted, as well as some minor systems. Currently, the only monitoring that is being done is battery temperature, and all monitoring done by off the shelf systems within their own system. None of this information is accessible without connecting a laptop to the various systems directly.

There are several different systems that need monitoring inside the EV. Primarily the HV (High Voltage) system requires monitoring of the temperature sensors for the compartments that hold the batteries. The temperature of the batteries affects the power output as well as the overall performance of the car. Other components include the accumulator isolation relays, fuse, current sensors, precharge and discharge system. The EV also requires monitoring of the LV (Low Voltage) systems as well as the status of the pedal control system.

The industry standards have several requirements for CAN protocols being utilized in road vehicles. Some of them include the following from ISO 11898:

- CAN specifies the high-speed physical media attachment (HS-PMA), including
HS-PMAs without and with low-power mode capability and those with selective wake-up functionality.
- CAN specifies characteristics of setting up an interchange of digital information between electronic control units of road vehicles equipped with CAN.

- CAN specifies the characteristics of setting up an interchange of digital information between modules implementing the protocol’s data link layer.

Being able to monitor, process, and display these systems statuses will be extremely beneficial for troubleshooting and overlay monitoring of the EV. The Formula SAE competition has very specific requirements regarding galvanic isolation of the HV and LV systems in the EV. These requirements need to be followed when developing our CAN system.

Data Flow Diagram

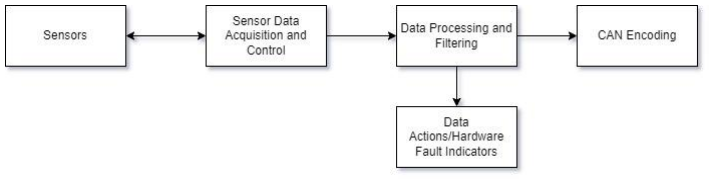
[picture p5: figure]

It is important to note that the VMS team has not utilized the CAN bus system for monitoring any sensor outputs in the past. However, even though the team has not implemented this system yet, there are several other off the shelf devices that utilize CAN to help monitor and also provide ability to alter the sensors and their calibration in order to get the best outcome from the overall system. Haltech offers a wide range of CAN Bus devices along with the sensors that are heavily used in the automotive industry, especially in DIY projects where factory engine management systems fail to deliver proper results. Research in companies like Haltech as well as other products like Vector used by Daimler can be beneficial for our project as well.

### 3. Project Overview

Our project starts with getting the STM32s to communicate with each other in order to relay information from one device to another. Each STM32 in our network will act as a CAN hub utilized to relay information from a specific component cluster on the vehicle. We then want to determine the protocols that allow data from the sensors to be received through the CAN transceivers.

We then have to design individual PCBs for each of the CAN hubs that hold the STM32s, the CAN transceivers and other peripheral components for the sensors to operate on the vehicle as well.

Using the STM32CubeIDE and C programming, we have to code each of the microcontrollers to log the data received from the CAN transceivers and relay them to the main Data Translator hub. The Data Translator further encodes the data to be read by a RaspberryPi via I²C which is used to display the data on the screen.

We want the CAN system to be able to collect sensor outputs from different components of the EV, send them to a central control hub, which processes the sensor readouts to legible information for the user and outputs to a screen via the CAN adapter.

### 4. Product Design Specification

### 4.1 Concept of Operation / User stories

Our goal for this project is to provide several different CAN modules that can be connected to different sensors on the EV components and the placement of these modules provides flexibility and easy integration along with the rest of the parts on the EV. Since the EV has restraints for weight and countless other things, the placement of our modules is very important. These modules are connected to the sensors on the vehicle and thus take the sensor readouts when the EV is operated. The CAN module thus sends the readouts to the central control hub which is another module that we create. This central hub encodes the sensor outputs and then sends them to the LCD display on the car via a CAN Adapter.

As mentioned earlier, these modules are constructed specifically for the VMS EV and would for the most part only work for our specific application since the placement on the devices, types of sensor, variation in sensor outputs and the process to encode them would vary from one vehicle to another. Thus the VMS team and their intermediate sponsors would be our main users and stakeholders in this project.

It is important to note that the vehicles built by the VMS team in the past have not had any CAN bus system utilized for monitoring and diagnostics. All previous troubleshooting was done in the event of a system failure and the panels had to be taken apart to look at the individual
components and sensors to determine the source of error. The CAN bus allows the electricians on the VMS team to simply use the LCD display and examine the readouts from the sensor in the event of the failure. This speeds the time it takes them to fix the car and get it back in the race at the FSAE competition. At the time the scope of our design concludes with relaying the data on the display screen. However, the project can be continued in the future to use the CAN Adapter to output the data logs to a laptop. There is also room in the future to be able to act upon the information received via CAN. For example, the ability to do system shutdown in the event of a component failure or out of range sensor reading can be a very effective addition to the overall safety of the vehicle.

In our case, since the sponsor is the primary user for our project, we want to follow the timeline of the rest of the EV build. Although we are not able to act upon the readouts we get from the sensor, we are merely monitoring them. However, there are products available in the market that allow for calibration and adjustment via USB connection to the CAN and sensors. This can be looked into upon future development of our project. Each of the CAN hubs will also act as data loggers as the microcontrollers will pull the data from the CAN bus, hold and store it.

As the rest of the members on the VMS team work on the other components that make the EV work, we want to work alongside their progress so as to make the integration of the CAN Bus more efficient and avoid any delays. We want the individual modules of the CAN Bus to be a plug and play system which can be routed along with the rest of the wiring on the EV. Although the design of the CAN Bus will be new for this year's EV, considering the fact that the VMS team has to build a new vehicle from scratch every year, they might be able to utilize some of the code and hardware and expand on the design of the CAN Bus for any future builds. Our goal is to create a smoothly integrated monitoring system system that is seamless with the rest of the EV build.

### 4.2 Stakeholders

Our project was proposed by Braedon Hamson, lead electrician on the VMS team. Him, along with several other key members on the team have been putting in countless hours in researching, developing, constructing, testing, and then improving the iterations of the EV. We are designing and constructing the CAN bus based on their requirements and working with them to create smooth integration of the CAN Bus into the EV. However we feel that there can be several other stakeholders in our project. The project team including Alice Ma , Braeden Hamson ,
Jade Nguyen , and Pushpesh Sharma , want to create something that leaves room for future growth and improvement. The EV inspectors that are part of the FSAE competition should also be considered solid stakeholders in this project as their judgment and criticism can be beneficial to the development of our project. But for the most part, the EV team at PSU will help integrate the CAN system, utilize it during the testing phase of the vehicle as well as on the track during the competition. Upon the success of this project, we hope that the VMS team is able to use the system for future use and add more features that helps the EV perform better in the upcoming competitions.

### 4.3 Requirements and Specifications

As mentioned earlier, we want to adhere to the requirements of the EV overall when designing and constructing our CAN Bus systems. We want to follow any necessary restraints set by the FSAE competition guidelines so as to avoid any delays and provide smooth integration of our systems with the rest of the vehicle. Thus most of our requirements for this project are based on the number of sensors and components that we want to read and monitor for the management of the EV. Other requirements are based on what components we utilize in our project in order to stay on budget and provide smooth integration when the time comes.

- Must be powered from 12V and/or 5V and tolerate a +/- 2V fluctuation
- When a board interacts with HV (350VDC) all HV components must be galvanically isolated from LV systems
- Must send data to a central data logging device connected to the CAN Bus
- Must use appropriate CAN Bus arbitration

- The team must cooperate with other members of the VMS team to ensure system compatibility
- Should follow accepted methods to protect devices on a CAN Bus
- Should use STM32 microcontrollers
- May monitor status of shutdown switches
- Should transmit data at a rate appropriate for the specific measurement
- Should monitor the following systems, in order of priority:
- AIR+, AIR-, and precharge signals
- APPS, BSPD, IMD, BMS OK, SDC status
- Tractive system voltage, tractive system current
- LV system voltages
- Orion BMS 2 data
■ Battery state of charge
■ Tractive system power output ■ Battery voltage
■ Battery current
- Cascadia Motion PM100DX data
■ Individual motor power
■ Inverter mode (running, fault, precharging etc.) ■ Relay outputs (used to detect wiring faults)

### 4.4 Deliverables

This critical section specs out what we are going to deliver to the industry sponsor by the end of your capstone. This must include:
- Project proposal
- Weekly Progress Reports
- Final Report
- ECE Capstone Poster Session poster
- Travel with the VMS team to Michigan to attend the FSAE competition. It is held on June 14-17 (travel and other expenses are covered)
- Detailed design documentation, explaining what the design does, how thedesign works, and why the team made the decisions it did
- Simulations, including both the simulation inputs and outputs
- Electrical CAD: Schematics and board layouts, including output files (Gerbers, PDFs, etc)
- Bill of materials and pricing
- Version control, including checked in previous revisions of your design (e.g., a Git repo).
- Individual PCBs with 3D printed housings for each of the boards.
- Functional code for STM32CubeIDE for the individual CAN hubs.

### 4.5 Initial product design

- Our current progress on this project consists of setting up software for the microcontroller that we will be using. We have decided to use STM32 along with the STM IDE to be able to take the sensor outputs from each component and then convert the values to send to the CAN Adapter which in the end gets displayed on the screen. We have also started working on the schematics for the PCBs that contain the STM32 microcontroller. These schematics contain the microcontroller itself along with the peripheral components that are necessary. We are also working on getting multiple STM32s to communicate with each other as the end goal would be to have several different boards placed in close proximity to the location of the sensor and have them send the sensor output to one main microcontroller board via CAN that processes the input and sends it to the CAN adapter.
- Hardware architecture

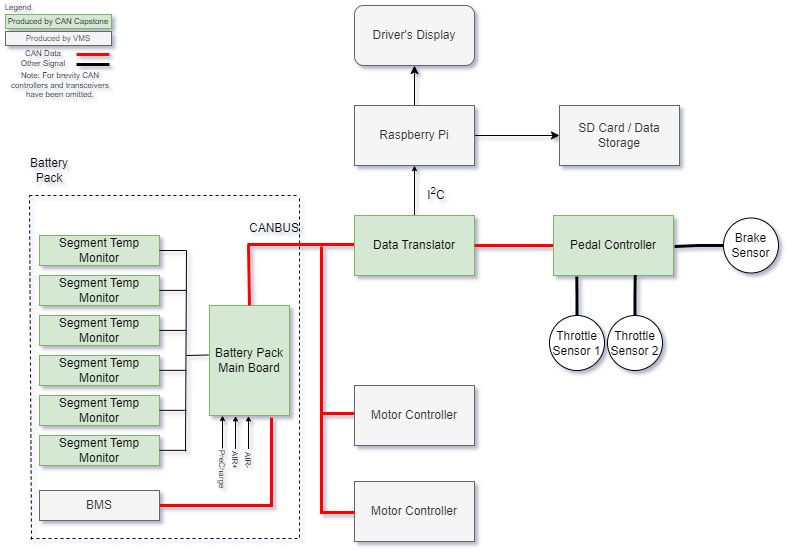
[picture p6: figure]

- Software architecture
- C, STM32CubeIDE

- User interface / experience

User Story: In the lab, the user is assembling the car, they test a certain feature and see that it does not function as intended. They can then go to the driver’s steering wheel, use the on-wheel controls to enter a maintenance menu that will display all measured parameters by the CAN system. They can then use this information to find the problem. For instance, the car is powered on, but HV will not engage. The user looks at the data from the wheel and sees that the pedal control board is indicating a signal out of range of the pedal controller. Investigating the sensor connections they find the sensor unplugged. They plug the sensor in and the system indicates the sensor is in range. The car then turns on.

- Other considerations

Electric vehicles are electrically noisy. Shielded wire will be used for long wire runs around the vehicle.

The battery pack contains up to 350V, galvanic isolation will separate the boards that are close to HV systems from the rest of the systems.

- Back up plans

The overall goal of this project is to create an easily debugged vehicle. If our plans totally crash and burn there’s nothing wrong with creating a 1960’s aesthetic by throwing a ton of blinking indicators around the car for debugging.

A step up from that is to use Arduinos and create a similar but less complex system for debugging.

The only aspect of this project that must be completed are the battery temperature monitors. Without this system the vehicle will not be allowed to race.

### 4.7 Verification plans

One of the biggest concerns with this project is the final integration of the CAN Bus with the rest of the components on the EV. We want to make sure that the system is able to successfully take the readouts from the sensors on the EV and encode them to be displayed on the screen. A lot of testing will be required to determine that the system is operating correctly.

The system will meet requirements if it can successfully read the temperature sensors in the battery modules and display them on the LCD. We may program the STM32s to encode the readout from the temperature sensors and determine whether it falls within the specific range for the battery to have optimal performance based on the requirements of the VMS team. Test: Does the LCD display the temperature of the specific battery module? Does it indicate when the temperature gets above a threshold range?

We are also going to test multiple STM32s to see if they can communicate with each other through the CAN network by sending messages from component A to component B, then from component B to component C, or until one goes to bus-off condition. we will determine if the system can analyze the error registers of the node as a means of measuring bus performance of a transceiver.

### 5. Project Management Plan

### 5.1 Timeline, with milestones

The timeline for our project needs to be aligned with that of the VMS team in order to finish the EV in time for the FSAE competition. Our sponsor wants to have a working CAN Bus system by the end of the ECE 412 course in order to leave ample time for system integration with the rest of the EV as well as the testing, and troubleshooting phases.

See Google Sheets below for a tentative timeline

Initial Gantt Chart for Capstone project - Google Sheets (https://docs.google.com/spreadsheets/d/1ESAUExDIhOSoRCvXFfbeXnNjUjRd7T-Y1ovpI8qUFuQ/edit#gid=0)

### 5.2 Budget and Resources

The budget for our project is combined with that of the overall VMS budget for the EV. Our main costs are going to dependent on the following:

- Number of STM32s used and their cost
- Cost of peripheral components for the microcontrollers
- Manufacturing costs of the PCBs for the STM32s and the peripheral components
- Wiring for the integrated boards via CAN.

The VMS team has kindly provided Altium to design the PCBS for the CAN modules. Most other components will be ordered from DigiKey or may already be available in the VMS inventories as they have been working on multiple vehicles in the past. The VMS team has also provided a work area along with the rest of the team members as resources for our project.

### 5.3 Intellectual Property Discussion

A goal of this capstone is to provide a framework to future teams to build more advanced CAN systems. Therefore all IP generated here will be completely open source, and will be readily available to future teams. The license used for the repository and the project overall is the GNU General Public License v3.0

### 5.4 Team and Development process

- Alice Ma: Project manager and Programming lead. Working on programming STM32 for sending and receiving CAN messages.
- Braeden Hamson: VMS electrical lead. CAN capstone technical lead. Understands the vehicle systems and the interface between the CAN system and the rest of the systems of the car.
- Jade Nguyen: working with Alice on setting up a CAN bus using the STM32 microcontroller, providing simple C code to read and write to the CAN bus and send it to the transceiver.
- Pushpesh Sharma: Working on PCB schematics and using Altium to set up schematics, footprints, PCB files and manufacturing files for several boards for CAN Bus.
- Collaboration tools: Notion for team tasking and note taking, Discord for every comms and virtual meetings, Github for code and boards, Google Suite for deliverables.

Faculty Advisor Approval

Advisor Name:_Roy Kravitz_

Signature:__e-approved by Roy Kravitz (rkravitz@pdx.edu)_

Date:__27-Feb-2023__

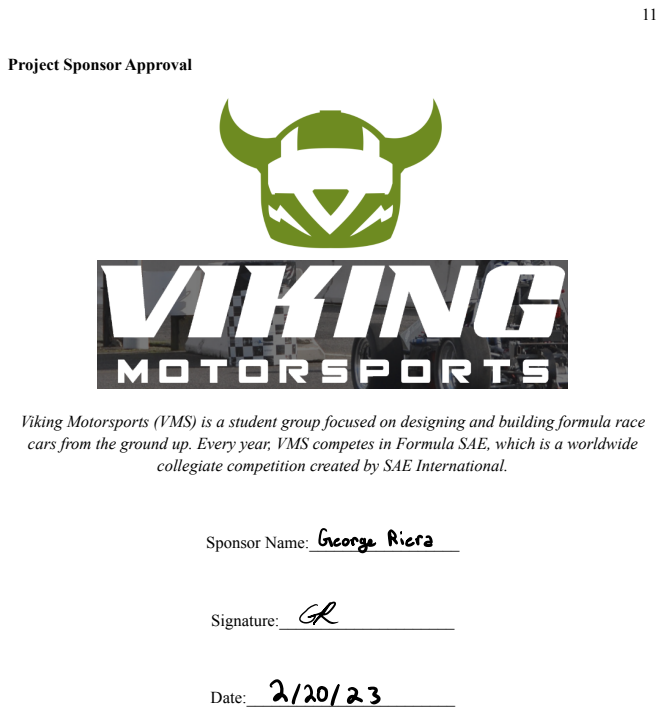
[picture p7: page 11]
Sponsor Name:__________________; Signature:_____________________; Date:_________________________; GeorgeRiera

Project Sponsor Approval

Viking Motorsports (VMS) is a student group focused on designing and building formula race
cars from the ground up. Every year, VMS competes in Formula SAE, which is a worldwide

collegiate competition created by SAE International.

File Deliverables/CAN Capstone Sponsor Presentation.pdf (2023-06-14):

# VMS CAN Bus Sensor Array Capstone

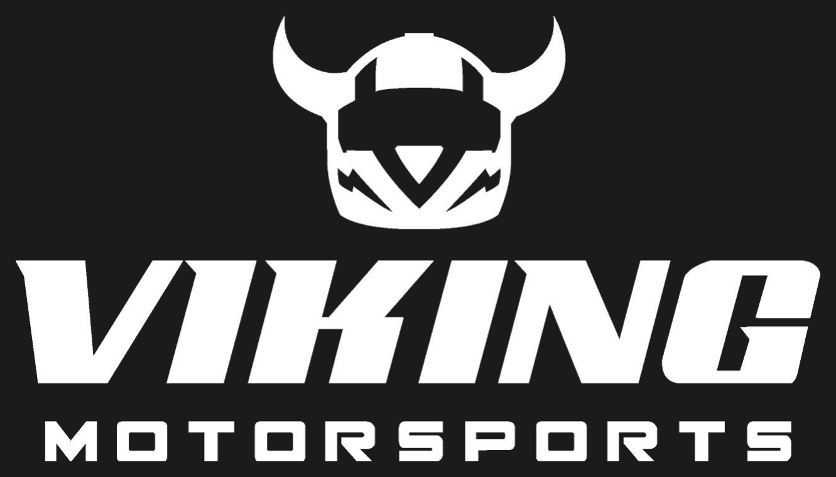
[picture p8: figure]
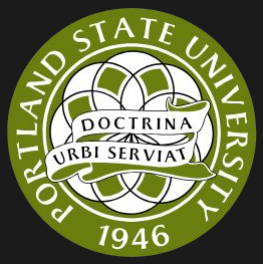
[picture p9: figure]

Portland State University

Alice Ma
Braeden Hamson
Jade Nguyen
Pushpesh Sharma

## In This Presentation

- Project background
- CAN overview
- STM32 overview
- Configuring CAN on the STM
- CAN physical construction and integration

## Problem

- Lack of system transparency leads to difficult debugging.
- Some testing has to be done near energized HV systems, by hand.
(With HV gloves)
- Extremely short testing times and race times means no time can be wasted on debugging systems.
- A wealth of data are contained in our off the shelf system’s CAN Bus’s
- System voltage, current, power, state of charge, battery temperature

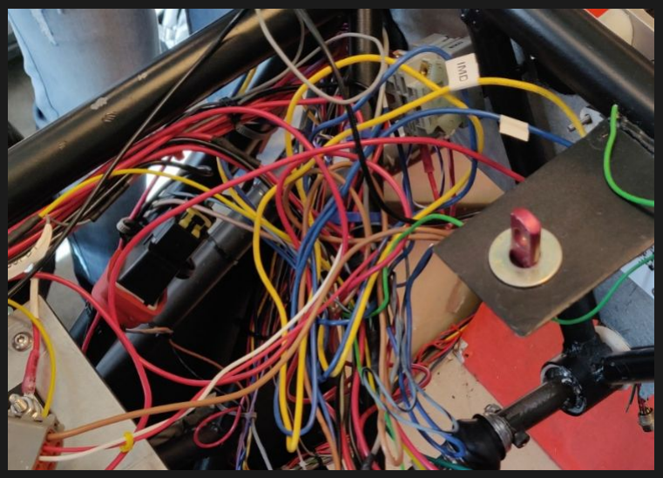
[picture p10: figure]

Previous wiring harness

## Project Goals

Increase the VMS team’s ability to locate electrical problems

## Methods to address the main goal

- Implement a CANBus
- Use STM32 microcontrollers
- Gather data and, important signals from key components of the car
- Motor Controller
- Battery Management System
- Accumulator (Main HV Battery)
- Pedal Monitoring Board
- Pass information from the CAN system to the driver’s display

## CAN Bus Overview

- Controller Area Network bus
- CAN is a serial protocol, like morse code
- CAN does not have a master-slave configuration, there is no central controller
- High reliability, robust
- Simple but deterministic arbitration of bus
- Extended to applications beyond automotive (i.e. truck, tractor, …) and industrial automation
- Many protocols in use that tailor the network for specific needs

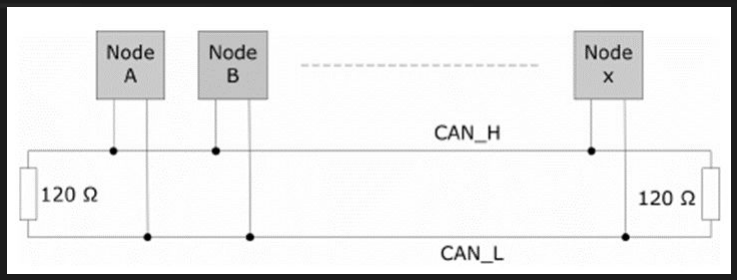
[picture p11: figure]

## Physical Layer

- 2 wire, differential signaling
- Speeds up to 1 Mb (length dependent)

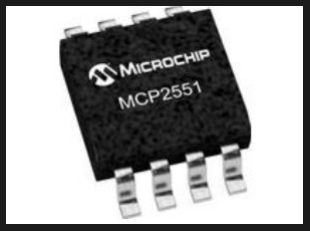
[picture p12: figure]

- Nodes, stubs called out in various specs
- Transmission line, so requires termination at ends
- “Built in” prioritization, arbitration and error detection

## CAN - Physical

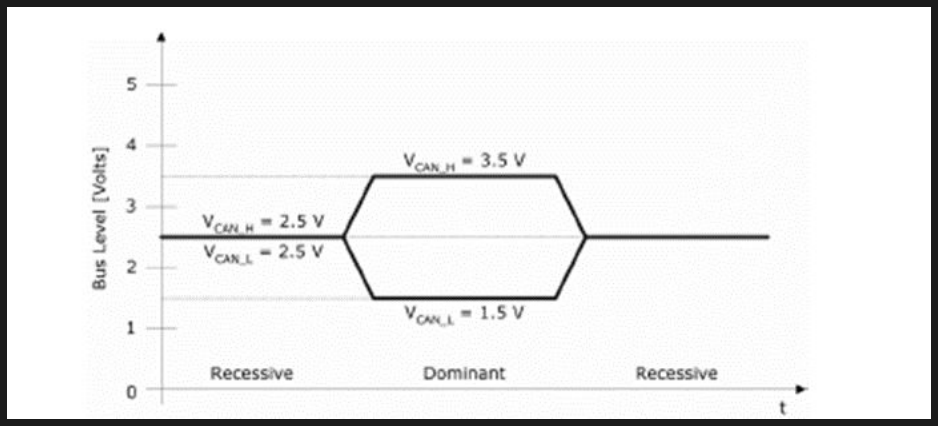
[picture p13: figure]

- Dominant – actively driven; Recessive – not driven

## Identifiers and message frames

Original (standard): 11 bit ID and 8 byte message (data) frame, with additional bits (ref 1)

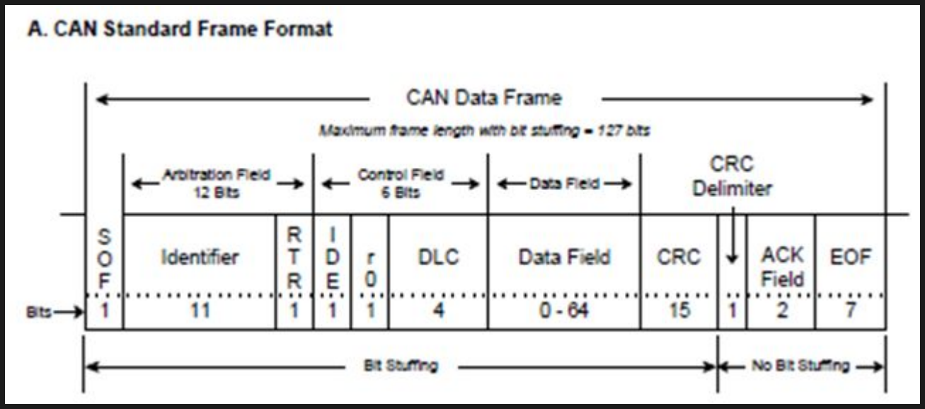
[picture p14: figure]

## Address Priority

The address of each node denotes it’s priority.

Lower addresses have a higher priority

Lower addresses have more dominant bits, a dominant bit will overrule a recessive bit

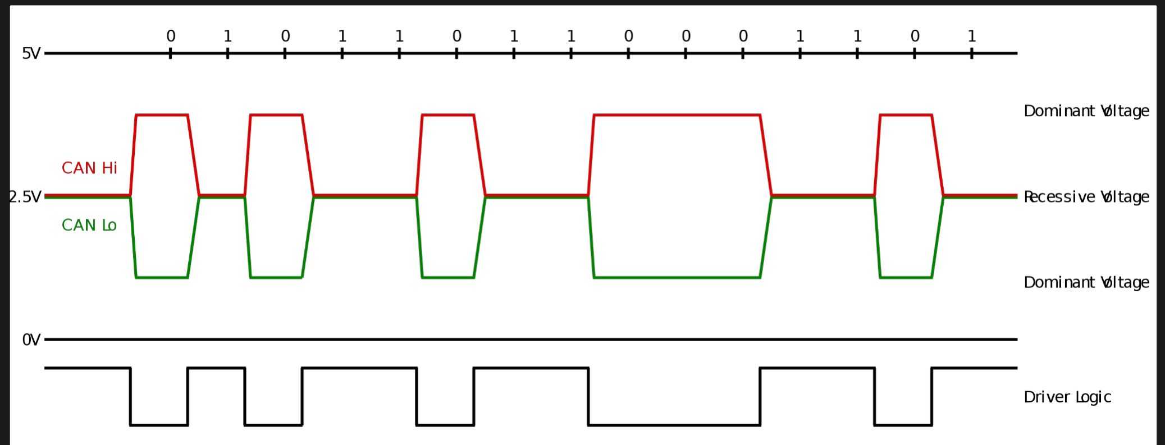
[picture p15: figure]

## CAN implementation on the car

- Data collected from each node on the car and distributed via CAN Bus.
- Specific PCBs created to collect information send to the next node.
- Altium Designer 22.10.1 used to create schematics and PCB layouts as well as manufacturing gerber files.

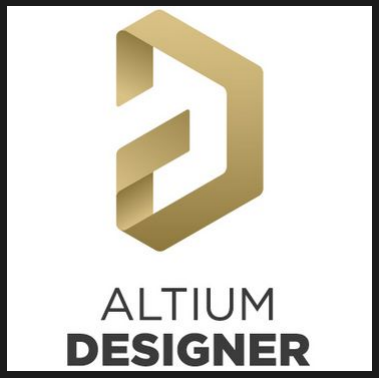
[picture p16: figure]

## CAN implementation on the car

- PCBs manufactured via JLC PCB and Oshpark
- PCBs then assembled using stencils when available
- Wiring harnesses created for all pinouts from schematics
- For testing purposes, the existing chassis was used to connect the boards and implement the CAN network

## Battery Segment Boards

- Collect temperature data from batteries and send to Accumulator Main Board via GPIO pins.
- Collect Voltage data and send to Battery Management Systems

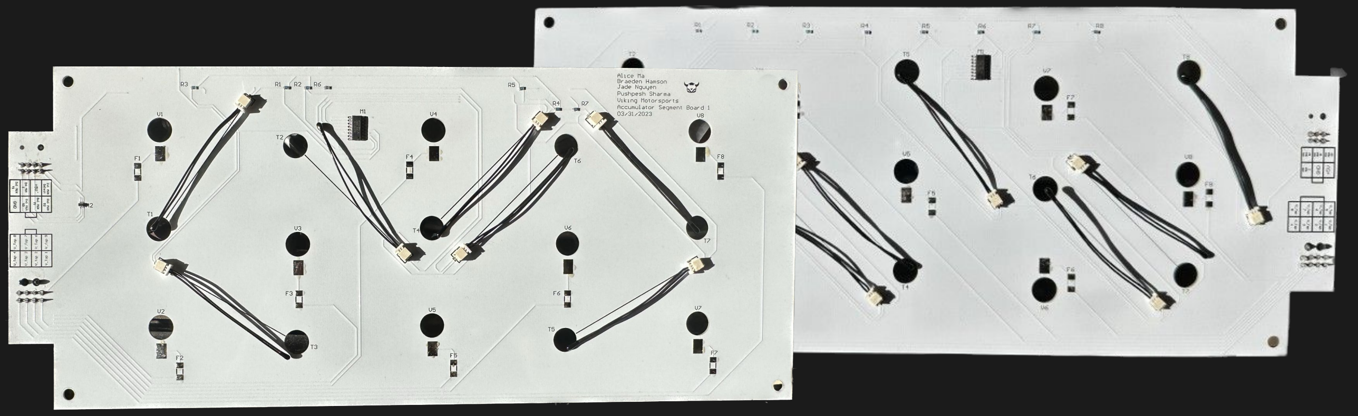
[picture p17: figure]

## Accumulator Main Board

- Receives temperature data from the Battery Segment boards through GPIO pins
- Receives and decodes CAN messages from Battery Management Systems
- Formats and sends the data received through CAN bus to the Data Translator Board.

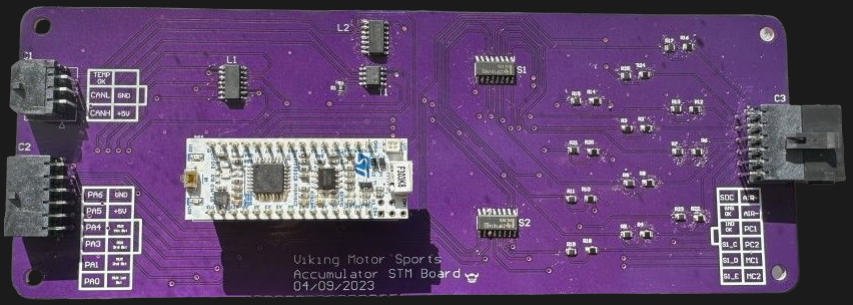
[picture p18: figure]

## Data Translator Board

- Receives CAN messages from accumulator board, pedal controller board, motor controller, and the BMS.
- Formats collected data from CAN and send it to Raspberry Pi through UART protocol

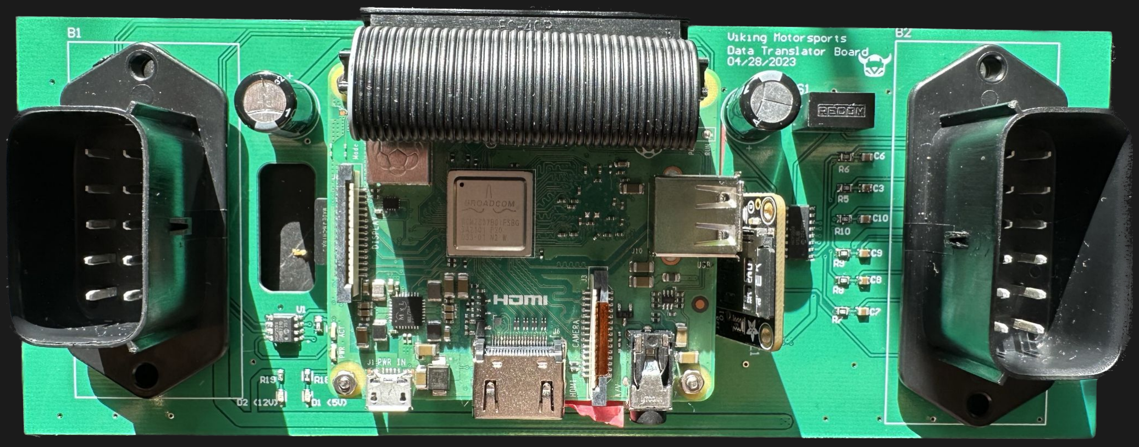
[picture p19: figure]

## Things that didn't go well with the boards

- Should have spent a longer amount of time double checking components, their placement, their footprints, and 3D layouts.
- Inaccurate components caused missing features and necessary bodging with jumper wires.
- Should have spent a longer amount of time organizing parts ordering to ensure availability of all components for each board.
- Should have been prepared to have at least one board revision to detect and fix any mistakes.

## Conclusion

CAN was successfully integrated into the existing chassis.

Data communication between each board was accurate.

Data is displayed onto screen successfully.

Our system is ready for any revisions and updates to be integrated into the future EV projects for the VMS team.

Questions?

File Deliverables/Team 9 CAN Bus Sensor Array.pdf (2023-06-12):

# VMS CAN Bus Sensor Array

Team: Alice Ma, Braeden Hamson, Jade Nguyen, Pushpesh Sharma | Faculty Advisor: Roy Kravitz | Industry Sponsor: Viking Motorsports

Deliver a network that uses CAN protocol to communicate system analytics from the car's batteries and several other measured components and relay that information to the driver’s display screen by converting CAN to UART.

Microcontroller: STM NUCLEO-F303K8 in a 32-pin package which has built-in CAN and UART capabilities. Programmed using CubeIDE firmware.
CAN Protocol: A method of communication between electronic devices embedded in a vehicle using a bus (high and low) that connects each node together.
UART Protocol: A hardware communication protocol that uses asynchronous serial communication with configurable speed.

### Accumulator Main Board

- Receives temperature data from the Battery Segment boards through GPIO pins
- Receives and decodes CAN messages from Battery Management Systems
- Formats and sends the data received through CAN bus to the Data Translator Board.
- Fabricated boards assembled and tested
- Individual wiring harnesses created for CAN bus and data collection from EV
- Boards and harnesses integrated into existing chassis.
- CAN communication coded and tested between each node.
- Data displayed on screen via Raspberry Pi

## MISSION

## Scan Me!

## OVERVIEW

## APPROACH

## PROTOTYPING & TESTING

## RESULTS

`

## PROJECT TIMELINE

January | February | March | April | May | June
Research Design Specification Software Setup | STM32 Setup Breadboarding PCB Schematics | PCB layouts CAN communication Component selection | PCB fabrication CAN filtering and further coding | PCB Assembly Code Freeze | Final Assembly Testing/Debugging Documentation

### Battery Segment Boards

- Collect temperature data from batteries and send to Accumulator Main Board via GPIO pins.
- Collect Voltage data and send to Battery Management Systems.

### Data Translator Board

- Receives CAN messages from accumulator board, pedal controller board, motor controller, and the BMS.
- Formats collected data from CAN and send it to Raspberry Pi through UART protocol.

## FUTURE WORK

- Need board revisions to fix mistakes and implement more features.
- Need full harness created around new Accumulator and updated chassis for FSAE Competition.
- Need more powerful microcontroller to handle CAN and UART at the same time.

Displays from
Raspberry Pi

CAN messages received

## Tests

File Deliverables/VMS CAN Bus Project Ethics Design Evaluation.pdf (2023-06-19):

### Design and Ethics Considerations

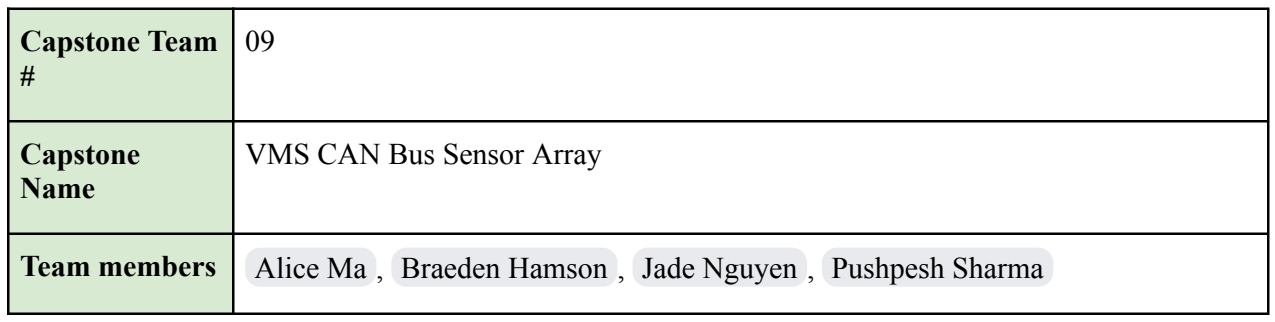
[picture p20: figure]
Capstone Team #; Capstone Name; VMS CAN Bus Sensor Array

Team members | Alice Ma , Braeden Hamson , Jade Nguyen , Pushpesh Sharma

Part 1: Design Considerations
- Public health, safety, and welfare
- Global factors
- Cultural factors
- Environmental factors
- Economic factors
Consider: | Yes/No/ Possibly | Why?
Public health, safety, and welfare | Yes | The implementation of CAN system can prevent dangerous operation of the EV that can result in a public safety event at a racetrack for example
Global factors | Yes | The parts that we spec and order from other countries affect our ability to collaborate with global vendors, and adapt to the time differences, language barriers, and other associated factors.
Cultural factors | Yes | How we work with our global vendors, how we work with the entire VMS team requires a clear understanding and requires our ability to adapt and respect cultural values of others and how they affect the way they react to conflict and how to perform overall.
Environmental factors | Yes | The overall EV project considers its environmental impact with the types of materials used and its environmental impact from global shipping requests as well as the positive impacts of being an emission free race car.
Economic factors | Yes | The budget of our capstone is dependent on the budget of the VMS team as a whole. All components used belong to the VMS team and should be utilized on the car. The availability of the certain components based on the current chip shortage as well as the cost of these components affects the number of features we may add onto our capstone.

Part 2: Ethics Considerations
- Global
- Economic
- Environmental
- Societal
Consider a context for ethical decision-making | Applicable: Yes/No/Possibly | Why?
Global | Yes | A motorsports team with multiple sponsors may or may not feel obligated to restrict its vendors and manufacturers to a local level to emphasize its origins.
Economic | Yes | Having local vendors might be beneficial to support local businesses but the cost can be significantly different from overseas options.
Environmental | Yes | The pivoting decision of the sponsor to move from combustion powered race car to an EV carries a lot of positive environmental factors that a lot of innovators and prospective sponsors can stand behind.
Societal | Yes | Creating an open ended project for other communities at Portland State University to use as motivation and a driving aid to get involved with teams like VMS and many others on campus.

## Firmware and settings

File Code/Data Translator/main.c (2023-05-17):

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
/* Includes ------------------------------------------------------------------*/
#include "main.h"

/* USER CODE BEGIN Includes */
#include <stdio.h>
#include <string.h>
#include "retarget.h"
/* USER CODE END Includes */

/* USER CODE BEGIN PD */
#define I2C_SLAVE_ADDR 0x20

/* USER CODE END PD */

CAN_HandleTypeDef hcan;

I2C_HandleTypeDef hi2c1;

UART_HandleTypeDef huart2;

/* USER CODE BEGIN PV */
CAN_RxHeaderTypeDef rxHeader; //CAN Bus Transmit Header
CAN_TxHeaderTypeDef txHeader; //CAN Bus Receive Header
uint8_t canRX[8] = {0,0,0,0,0,0,0,0};  //CAN Bus Receive Buffer
CAN_FilterTypeDef canfil; //CAN Bus Filter
uint32_t canMailbox; //CAN Bus Mail box variable

/*I2C*/
uint8_t buff[8];
uint8_t transmittingBufferDataSize = 8;
char logg[100];
uint16_t log_len;
int loop;
/* USER CODE END PV */

void SystemClock_Config(void);
static void MX_GPIO_Init(void);
static void MX_USART2_UART_Init(void);
static void MX_CAN_Init(void);
static void MX_I2C1_Init(void);
/**
  * @brief  The application entry point.
  * @retval int
  */
int main(void)
{
  /* MCU Configuration--------------------------------------------------------*/

  /* Reset of all peripherals, Initializes the Flash interface and the Systick. */
  HAL_Init();

  /* Configure the system clock */
  SystemClock_Config();

  /* Initialize all configured peripherals */
  MX_GPIO_Init();
  MX_USART2_UART_Init();
  MX_CAN_Init();
  MX_I2C1_Init();
  /* USER CODE BEGIN 2 */
  RetargetInit(&huart2);

  canfil.FilterBank = 0;
  canfil.FilterMode = CAN_FILTERMODE_IDMASK;
  canfil.FilterFIFOAssignment = CAN_RX_FIFO0;
  canfil.FilterIdHigh = 0;
  canfil.FilterIdLow = 0;
  canfil.FilterMaskIdHigh = 0;
  canfil.FilterMaskIdLow = 0;
  canfil.FilterScale = CAN_FILTERSCALE_32BIT;
  canfil.FilterActivation = ENABLE;

  txHeader.DLC = 8;
  txHeader.IDE = CAN_ID_STD;
  txHeader.RTR = CAN_RTR_DATA;
  txHeader.StdId = 0x453;
  txHeader.ExtId = 0x02;
  txHeader.TransmitGlobalTime = DISABLE;

  HAL_I2C_EnableListen_IT(&hi2c1);

  HAL_CAN_ConfigFilter(&hcan,&canfil);
  HAL_CAN_Start(&hcan);
  if (HAL_CAN_ActivateNotification(&hcan, CAN_IT_RX_FIFO0_MSG_PENDING) != HAL_OK)
  {
  	  Error_Handler();
  }
  /* USER CODE END 2 */

  /* Infinite loop */
  /* USER CODE BEGIN WHILE */
  while (1)
  {


    /* USER CODE END WHILE */

    /* USER CODE BEGIN 3 */
  }
  /* USER CODE END 3 */
}

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
/* USER CODE BEGIN 4 */


void HAL_CAN_RxFifo0MsgPendingCallback(CAN_HandleTypeDef *hcan){
	   	if (HAL_CAN_GetRxMessage(hcan, CAN_RX_FIFO0, &rxHeader, canRX) != HAL_OK)
	  	{
	  		Error_Handler();
	  	}

	   	memcpy(buff, canRX,8);
	  	//HAL_GPIO_TogglePin(GPIOB, GPIO_PIN_3);

	  	for(loop = 0; loop < 8; loop++)
	  		printf("%d ", canRX[loop]);
	  	printf("\r\n");


	  	printf("%x", rxHeader);
	  	printf("\r\n");


}

void HAL_I2C_AddrCallback(I2C_HandleTypeDef *hi2c, uint8_t transferDirection, uint16_t addressMatchCode) {

	/*buff[0]=0;
	buff[1]=1;
	buff[2]=2;
	buff[3]=3;
	buff[4]=4;
	buff[5]=5;
	buff[6]=6;
	buff[7]=7;*/

	printf("before transmit: ");
  	for(loop = 0; loop < 8; loop++)
  		printf("%d ", buff[loop]);
  	printf("\r\n");

	if (HAL_I2C_Slave_Seq_Transmit_IT(hi2c, buff, 8, I2C_LAST_FRAME) != HAL_OK)
	{
		Error_Handler();
	}

}
void HAL_I2C_ListenCpltCallback(I2C_HandleTypeDef *hi2c) {

    HAL_I2C_EnableListen_IT(&hi2c1);
}

void HAL_I2C_SlaveTxCpltCallback(I2C_HandleTypeDef *hi2c) {

	HAL_GPIO_TogglePin (GPIOB, GPIO_PIN_3);
	log_len = sprintf(logg, "I2C Slave Data: %d, %d, %d, %d, %d, %d, %d, %d\r\n", buff[0], buff[1], buff[2], buff[3], buff[4], buff[5], buff[6], buff[7]);
	HAL_UART_Transmit(&huart2, (uint8_t *)logg, log_len, 10);
}


/* USER CODE END 4 */
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


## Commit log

2023-04-19 Create Board Files
2023-04-20 Verison 1 I2C master transmit
2023-04-28 Slave I2C / CAN Receiver
2023-05-17 Create main.c
    version: receives CAN and sends I2C (does not work)
    [main.c]

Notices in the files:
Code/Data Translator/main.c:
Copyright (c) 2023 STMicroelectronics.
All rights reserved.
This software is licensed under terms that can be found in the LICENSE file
